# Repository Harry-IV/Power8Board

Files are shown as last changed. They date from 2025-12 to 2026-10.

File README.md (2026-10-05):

# Power8Board V1

48V → 12V Power Distribution & Current-Sensing Board for 8 Thrusters

## Overview

Power8Board is a custom power distribution and sensing PCB intended for robotics applications (e.g. ROVs / AUVs) where 6 DoF control is needed from eight thrusters. 

The board converts 48V DC into 5V and 12V rails, distributes power to eight ESCs, and provides per-thruster current measurement and voltage rail monitoring (3.3, 5, 12, 48) over I²C.

---

## Power Architecture

Two [MPQ860-12V72-L48NBMC](https://www.digikey.com/en/products/detail/murata-power-solutions-inc/MPQ860-12V72-L48NBMC/26005878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) 860W power converters are used to step down 48 to 12V with high efficiency. This 12V power is then routed to eight XT30U-M connectors which ESCs can then connect to for power. These were chosen due to having four power pins, allowing for better heat distribution, and for their active current sharing capabilities. With ~1500W (not 1720 due to drop in max wattage output when current sharing), eight standard T200 thrusters can be driven at full power. This 12V can also be used to power other 12V devices using the [MR30 connector](https://www.tme.com/us/en-us/details/mr30pw-m/dc-power-connectors/amass/) on the board. 

Additionally, a [UWS-5/10-Q48N-C](https://www.digikey.com/en/products/detail/murata-power-solutions-inc/UWS-5-10-Q48N-C/3041704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) 100W power converter is used to step down 48V to 5V. This 5V is outputted through the MR30 and can be used to power a Raspberry Pi for instance.

---

## Current Sensing

Monitor thruster load and detect abnormal conditions (e.g. over-current):

### Current-Sense Amplifiers
  * [INA240A2](https://www.ti.com/product/INA240) (analog)
  * One per ESC channel
  * 50x amplification value (50V/V gain)
* 0.0033 $\Omega$ shunt resistor placed in series with each 12V output
  * Scale factor: 1 / (SHUNT_VALUE * AMP_FACTOR) = 1 / (0.0033 * 50) = 6.061
  * current = 6.061 * (output of INA240)
* Analog output routed to ADC inputs with RC-filter (680 $\Omega$, 2.2 uF)

### Channel Organization

* Left side: 4 thrusters
* Right side: 4 thrusters
* Each side feeds into its own ADC, an [ADS1015](https://www.ti.com/product/ADS1015) (12-bit, I²C interfacing)
* I²C address:
  * Left: 0x48
  * Right: 0x49

---

## Voltage Sensing

Monitor that voltage rails are within normal bounds.

### Power Rails

| Rail  | Purpose |
| ----- | --- |
| 48 V  | Main input power |
| 12 V  | ESC & thruster power |
| 5 V | Miscellaneous |
| 3.3 V | ADCs, current sensors, I²C |

### ADC

* [ADS1015](https://www.ti.com/product/ADS1015) (12-bit, I²C interfacing)
  * Used for measuring the voltages
  * Address: 0x4A

### Voltage Dividers



### Scalar Values
  * 48V: (470+25)/25 = 19.8
  * 12V: (470+110)/110 = 5.273
  * 5V: (470+470)/470 = 2
  * 3.3V: (470+470)/470 = 2

Multiply these values read from the ADC by these scalars respectively to find their true voltages.

---

## LED Indicators

| Rail  | Color |
| ----- | --- |
| 48 V  | Green |
| 12 V  | Yellow |
| 5 V | Red |
| 3.3 V | Amber |

---

## PCB Layout

### 6-layer stackup

| Layer | Type |
| ----- | --- |
| 1 | Signal |
| 2 | Ground |
| 3 | Signal - Power (3.3V) |
| 4 | Power (12V & 48V) |
| 5 | Ground |
| 6 | Signal |



### Design notes

* Nearly all analog traces are routed on layer 3 to reduce effects of digital noise.
* Copper pours help with thermal dissipation.
* Via-in-pad is used to condense routing. It's also a standard option for 6-layer boards when ordering with JLCPCB.
* Ground on layer 2 & 5 provides low-impedance return path and reduce EMI.
* Power converters connect from the backside. 

---

## Ordering

To order, navigate to Power8Board V1/Export. Use Power8Board V1.zip for ordering the PCB and Power8Board V1 Stencil.zip for ordering a stencil (very helpful for soldering). Here are the options I chose when ordering from JLCPCB:



For ordering the components, navigate to Power8Board V1/bom and click on ibom.html. This BOM is interactive, making it great for ordering and knowing where components go while soldering. **Note that this does not include all components for making the board.** This is because pin receptacles are soldered onto the pads for all power converters. Here are the two types of pin receptacles used on the board:

Pin #1: https://www.digikey.com/en/products/detail/mill-max-manufacturing-corp/0372-0-15-15-13-27-10-0/433860

Pin #2: https://www.digikey.com/en/products/detail/mill-max-manufacturing-corp/0312-0-15-15-34-27-10-0/433567

Pin #1 is used on pads 4, 5, 7, and 8 on both 48V-12V converters and on pads 4 and 8 on the 48V-5V converter (10 in total)

Pin #2 is used on pads 1, 2, and 3 on both 48V-12V converters and on pads 1, 2, 3, 5, 6, and 7 on the 48V-5V converter (12 in total)

---

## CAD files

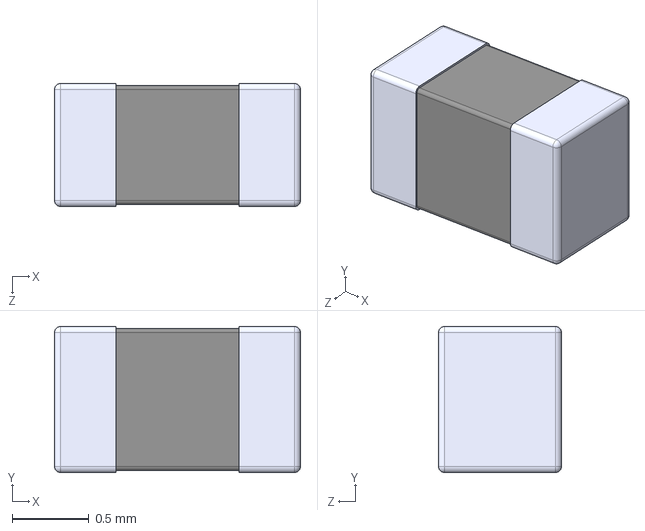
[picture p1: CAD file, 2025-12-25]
Power8Board V1/Components/0603 Ferrite Bead/BLM18KG102SZ1D.step
1.60 x 0.95 x 0.8 mm

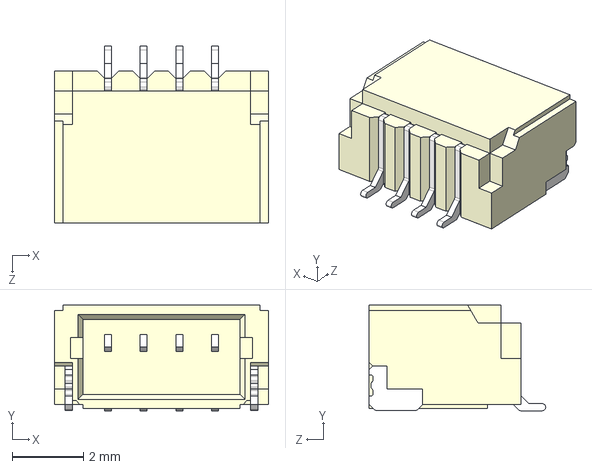
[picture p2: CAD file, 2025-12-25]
Power8Board V1/Components/QWIIC Connector RA/QWIIC Connector RA.step
6.00 x 2.96 x 4.95 mm

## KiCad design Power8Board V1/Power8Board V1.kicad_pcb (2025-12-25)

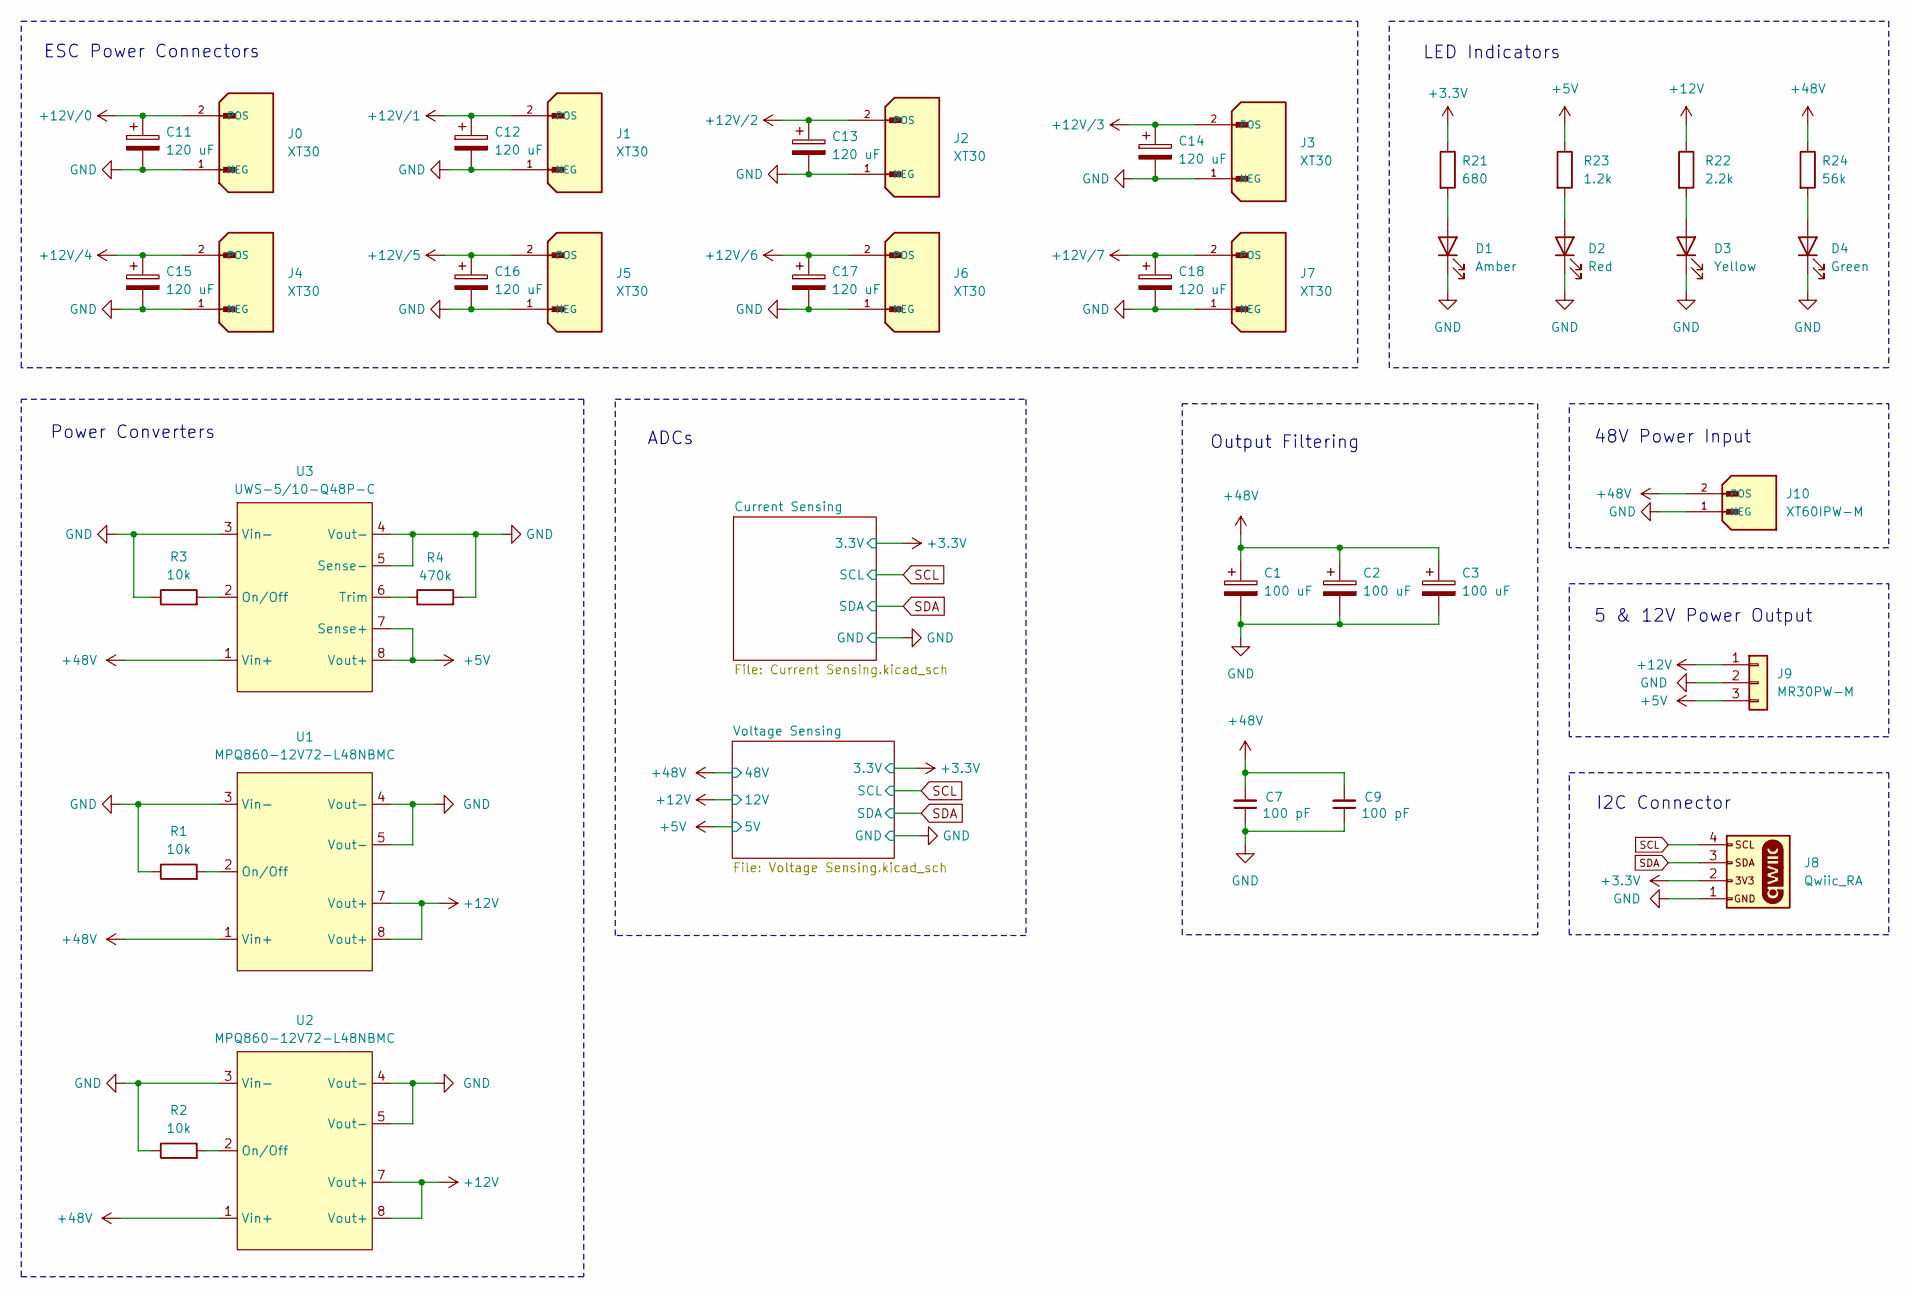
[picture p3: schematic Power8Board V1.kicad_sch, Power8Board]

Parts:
C1, C2, C3: 100 uF; CAP_AVG-8x12_ILC; Part # 107AVG063MFBJ
C7, C9: 100 pF; CAPC2012X140N; Part # KGQ21HCG2A101JT
C11, C12, C13, C14, C15, C16, C17, C18: 120 uF; PCAP_SVP_C6_PAN-M; Part # 20SVPF120M
D1: Amber; WL-SMCW_0805; Part # 150080AS75000
D2: Red; WL-SMCW_0805; Part # 150080RS75000
D3: Yellow; WL-SMCW_0805; Part # 150080YS75000
D4: Green; WL-SMCW_0805; Part # 150080GS75000
J0, J1, J2, J3, J4, J5, J6, J7: XT30; AMASS_XT30U-M_1x02_P5.0mm_Vertical; Part # XT30U-M
J8: Qwiic_RA; QWIIC Connector RA; Part # SM04B-SRSS-TB
J9: MR30PW-M; AMASS_MR30PW-M_1x03_P3.50mm_Horizontal; Part # MR30PW-M
J10: XT60IPW-M; AMASS_XT60IPW-M_1x03_P7.20mm_Horizontal; Part # XT60IPW-M
R1, R2, R3: 10k; R_0805_2012Metric; Part # CRGCQ0805F10K
R4: 470k; R_0805_2012Metric; Part # CRGCQ0805F470K
R21: 680; R_0805_2012Metric; Part # CRGCQ0805F680R
R22: 2.2k; R_0805_2012Metric; Part # CRGCQ0805F2K2
R23: 1.2k; R_0805_2012Metric; Part # CRGCQ0805F1K2
R24: 56k; R_0805_2012Metric; Part # CRGCQ0805F56K
U1, U2: MPQ860-12V72-L48NBMC; Part # MPQ860-12V72-L48NBMC
U3: UWS-5_10-Q48; Part # UWS-5/10-Q48P-C

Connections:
+3.3V: J8.2, R21.1; also elsewhere on the board
+5V: J9.3, R23.1, U3.7 (Sense+), U3.8 (Vout+); also elsewhere on the board
+12V: J9.1, R22.1, U1.7 (Vout+), U1.8 (Vout+), U2.7 (Vout+), U2.8 (Vout+); also elsewhere on the board
+12V/0: C11.1, J0.2 (POS); also elsewhere on the board
+12V/1: C12.1, J1.2 (POS); also elsewhere on the board
+12V/2: C13.1, J2.2 (POS); also elsewhere on the board
+12V/3: C14.1, J3.2 (POS); also elsewhere on the board
+12V/4: C15.1, J4.2 (POS); also elsewhere on the board
+12V/5: C16.1, J5.2 (POS); also elsewhere on the board
+12V/6: C17.1, J6.2 (POS); also elsewhere on the board
+12V/7: C18.1, J7.2 (POS); also elsewhere on the board
+48V: C1.1, C2.1, C3.1, C7.2, C9.2, J10.2 (POS), R24.1, U1.1 (Vin+), U2.1 (Vin+), U3.1 (Vin+); also elsewhere on the board
GND: C1.2, C2.2, C3.2, C7.1, C9.1, C11.2, C12.2, C13.2, C14.2, C15.2, C16.2, C17.2, C18.2, D1.1 (K), D2.1 (K), D3.1 (K), D4.1 (K), J0.1 (NEG), J1.1 (NEG), J2.1 (NEG), J3.1 (NEG), J4.1 (NEG), J5.1 (NEG), J6.1 (NEG), J7.1 (NEG), J8.1, J9.2, J10.1 (NEG), R1.1, R2.1, R3.1, R4.2, U1.3 (Vin-), U1.4 (Vout-), U1.5 (Vout-), U2.3 (Vin-), U2.4 (Vout-), U2.5 (Vout-), U3.3 (Vin-), U3.4 (Vout-), U3.5 (Sense-); also elsewhere on the board
unnamed: D1.2 (A), R21.2
unnamed: D2.2 (A), R23.2
unnamed: D3.2 (A), R22.2
unnamed: D4.2 (A), R24.2
unnamed: R1.2, U1.2 (On/Off)
unnamed: R2.2, U2.2 (On/Off)
unnamed: R3.2, U3.2 (On/Off)
unnamed: R4.1, U3.6 (Trim)
SCL: J8.4; also elsewhere on the board
SDA: J8.3; also elsewhere on the board

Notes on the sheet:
I2C Connector
LED Indicators
48V Power Input
ADCs
Power Converters
Output Filtering
5 & 12V Power Output
ESC Power Connectors

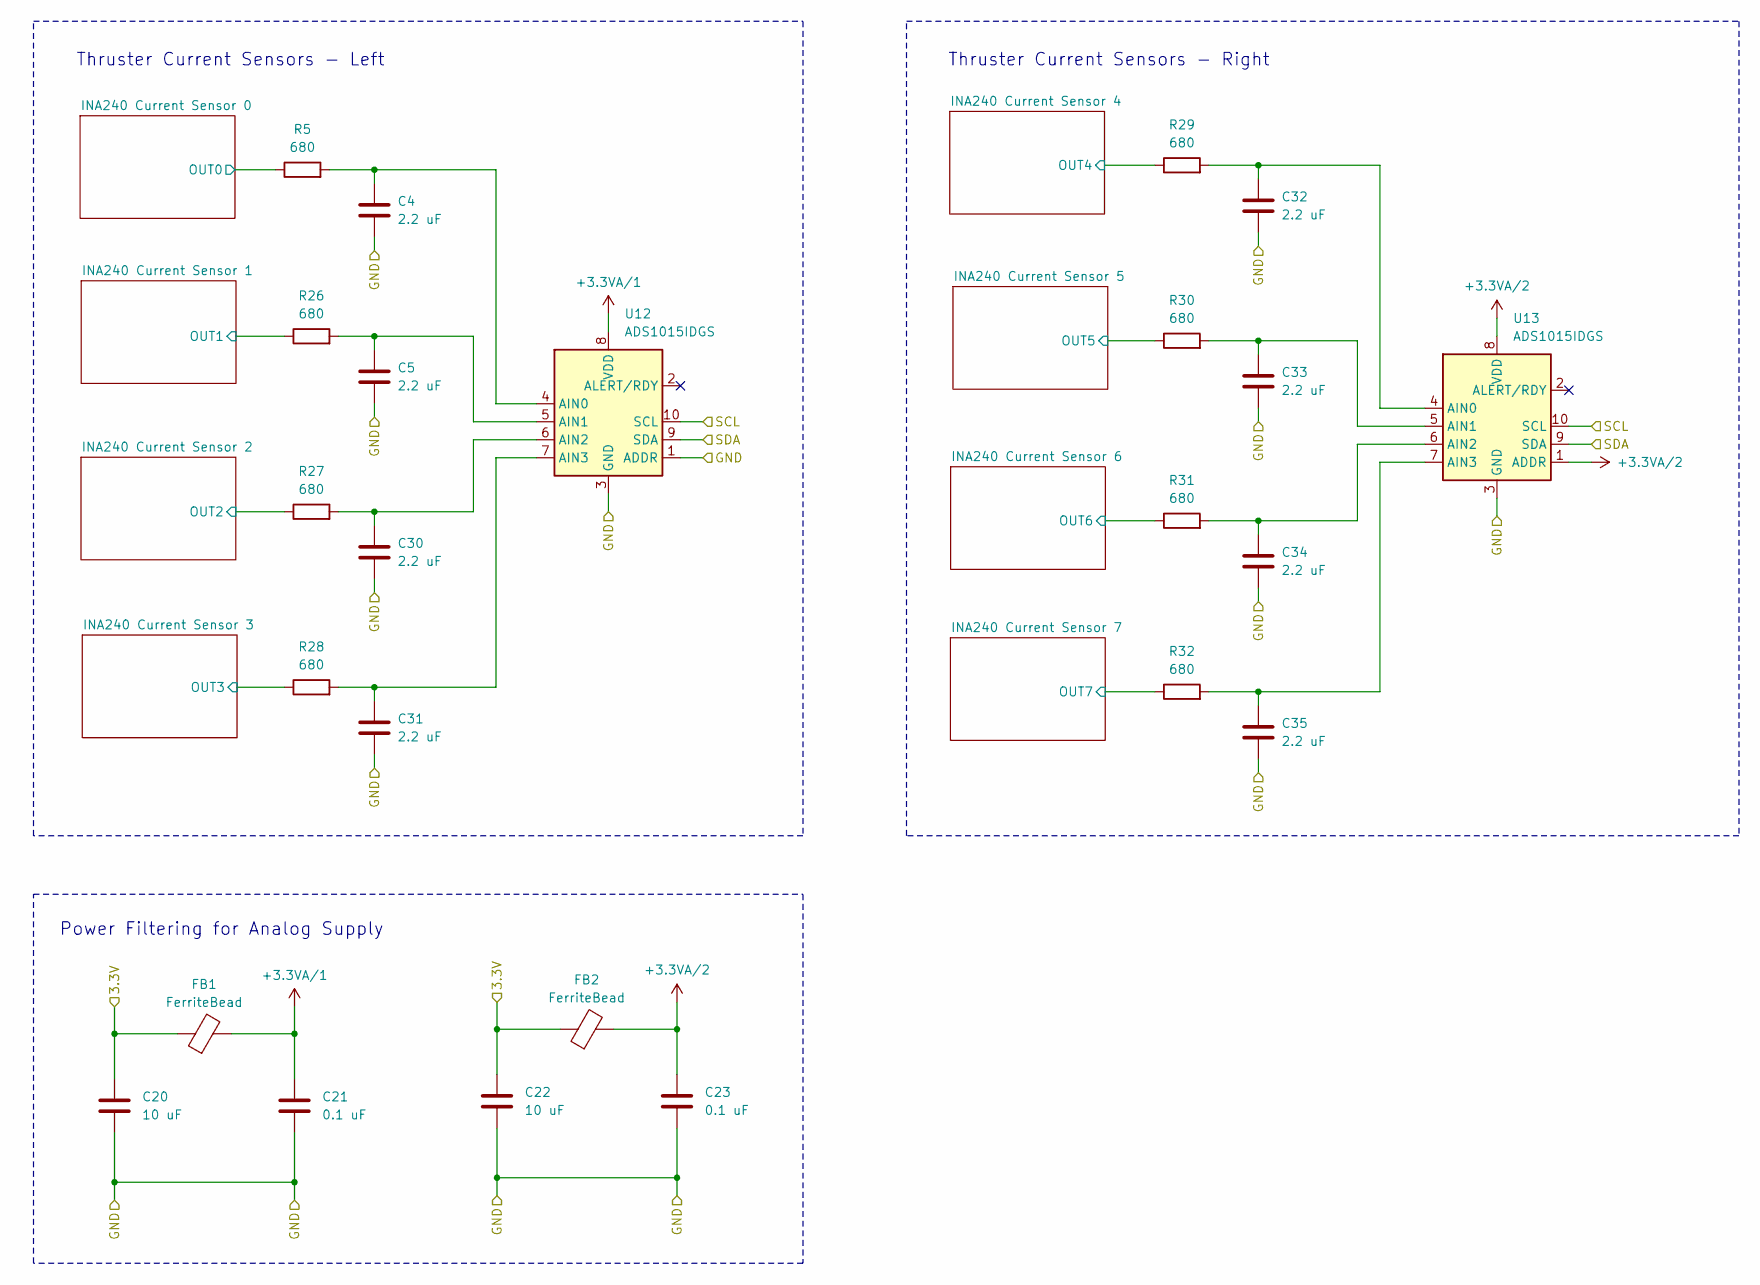
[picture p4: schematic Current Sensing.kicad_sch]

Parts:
C4, C5, C30, C31, C32, C33, C34, C35: 2.2 uF; C_0603_1608Metric; Part # GRM188Z71E225KE43D
C20, C22: 10 uF; C_0603_1608Metric; Part # GRM188R61E106KA73D
C21, C23: 0.1 uF; C_0603_1608Metric; Part # C0603C104K5RACTU
FB1, FB2: FerriteBead; 0603 Ferrite Bead; Part # BLM18KG102SZ1D
R5, R26, R27, R28, R29, R30, R31, R32: 680; R_0603_1608Metric; Part # CRGCQ0603F680R
U12, U13: ADS1015IDGS; TSSOP-10_3x3mm_P0.5mm; Part # ADS1015IDGSR

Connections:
+3.3V: C20.1, C22.1, FB1.1, FB2.1; also elsewhere on the board
+3.3VA/1: C21.1, FB1.2, U12.8 (VDD)
+3.3VA/2: C23.1, FB2.2, U13.1 (ADDR), U13.8 (VDD)
/Current Sensing/INA240 Current Sensor 0/OUT0: R5.1; also elsewhere on the board
/Current Sensing/INA240 Current Sensor 1/OUT1: R26.1; also elsewhere on the board
/Current Sensing/INA240 Current Sensor 2/OUT2: R27.1; also elsewhere on the board
/Current Sensing/INA240 Current Sensor 3/OUT3: R28.1; also elsewhere on the board
/Current Sensing/INA240 Current Sensor 4/OUT4: R29.1; also elsewhere on the board
/Current Sensing/INA240 Current Sensor 5/OUT5: R30.1; also elsewhere on the board
/Current Sensing/INA240 Current Sensor 6/OUT6: R31.1; also elsewhere on the board
/Current Sensing/INA240 Current Sensor 7/OUT7: R32.1; also elsewhere on the board
GND: C4.2, C5.2, C20.2, C21.2, C22.2, C23.2, C30.2, C31.2, C32.2, C33.2, C34.2, C35.2, U12.1 (ADDR), U12.3 (GND), U13.3 (GND); also elsewhere on the board
unnamed: C4.1, R5.2, U12.4 (AIN0)
unnamed: C5.1, R26.2, U12.5 (AIN1)
unnamed: C30.1, R27.2, U12.6 (AIN2)
unnamed: C31.1, R28.2, U12.7 (AIN3)
unnamed: C32.1, R29.2, U13.4 (AIN0)
unnamed: C33.1, R30.2, U13.5 (AIN1)
unnamed: C34.1, R31.2, U13.6 (AIN2)
unnamed: C35.1, R32.2, U13.7 (AIN3)
SCL: U12.10 (SCL), U13.10 (SCL); also elsewhere on the board
SDA: U12.9 (SDA), U13.9 (SDA); also elsewhere on the board

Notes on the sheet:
Thruster Current Sensors - Right
Power Filtering for Analog Supply
Thruster Current Sensors - Left

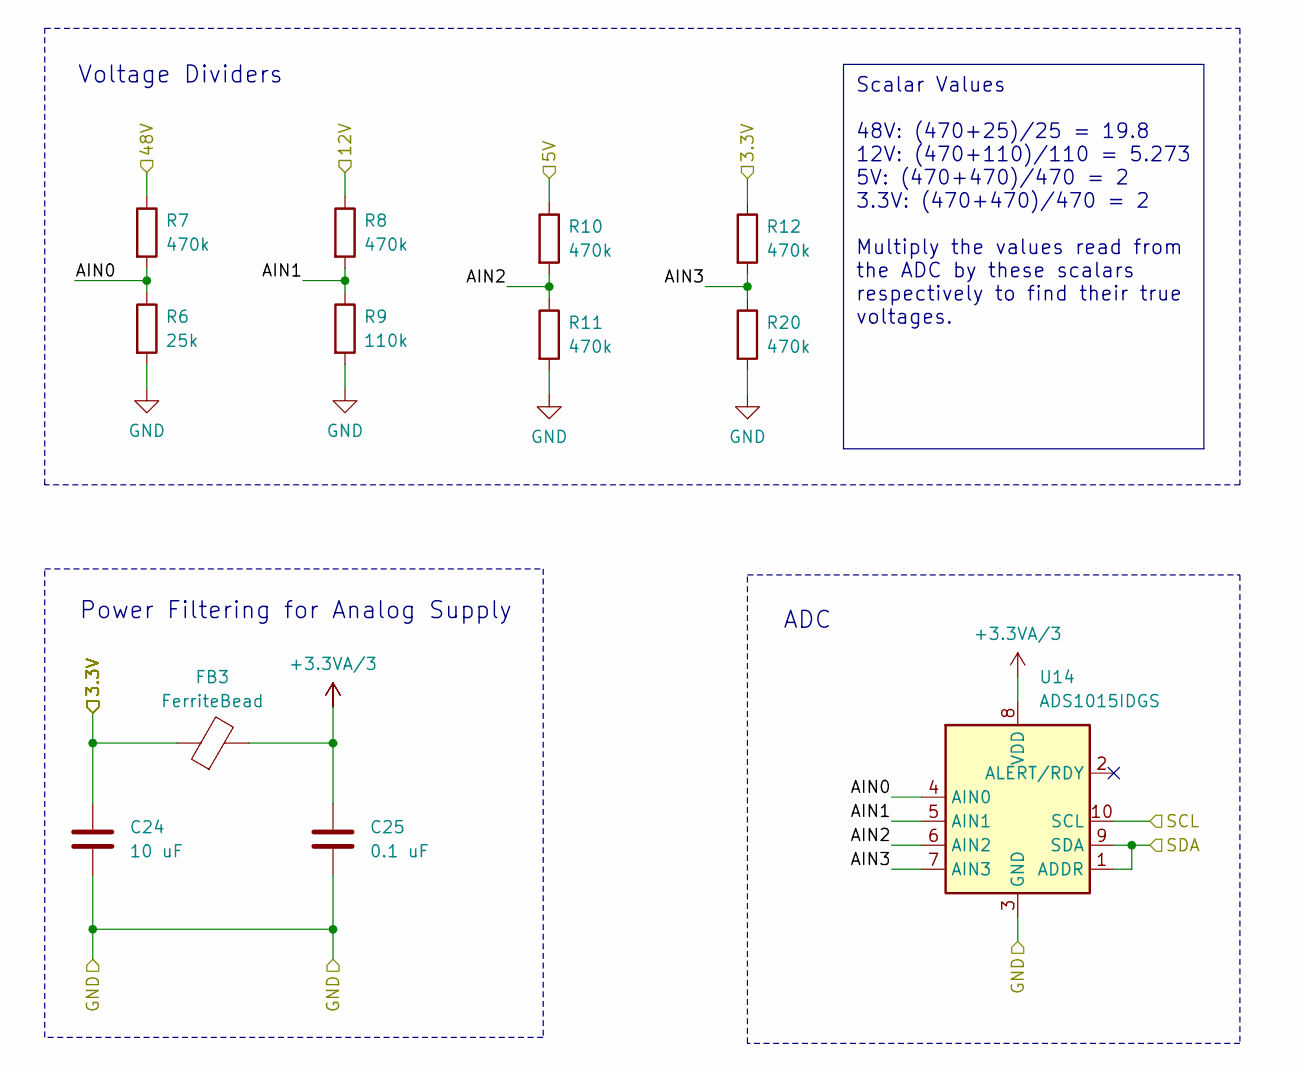
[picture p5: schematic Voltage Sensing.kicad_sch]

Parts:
C24: 10 uF; C_0805_2012Metric; Part # GRT21BC71E106KE13L
C25: 0.1 uF; C_0805_2012Metric; Part # C0805C104J5RACAUTO
FB3: FerriteBead; BEADC2012X105N; Part # MPZ2012S102ATD25
R6: 25k; R_0805_2012Metric; Part # CPF-A-0805B25KE
R7, R8, R10, R11, R12, R20: 470k; RES_TNPW0805_VIS; Part # TNPW0805470KBEEA
R9: 110k; R_0805_2012Metric; Part # RQ73C2A110KBTDF
U14: ADS1015IDGS; TSSOP-10_3x3mm_P0.5mm; Part # ADS1015IDGSR

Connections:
+3.3V: C24.1, FB3.1, R12.1; also elsewhere on the board
+3.3VA/3: C25.1, FB3.2, U14.8 (VDD)
+5V: R10.1; also elsewhere on the board
+12V: R8.1; also elsewhere on the board
+48V: R7.1; also elsewhere on the board
/Voltage Sensing/AIN0: R6.1, R7.2, U14.4 (AIN0)
/Voltage Sensing/AIN1: R8.2, R9.1, U14.5 (AIN1)
/Voltage Sensing/AIN2: R10.2, R11.1, U14.6 (AIN2)
/Voltage Sensing/AIN3: R12.2, R20.1, U14.7 (AIN3)
GND: C24.2, C25.2, R6.2, R9.2, R11.2, R20.2, U14.3 (GND); also elsewhere on the board
SCL: U14.10 (SCL); also elsewhere on the board
SDA: U14.1 (ADDR), U14.9 (SDA); also elsewhere on the board

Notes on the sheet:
Scalar Values 48V: (470+25)/25 = 19.8 12V: (470+110)/110 = 5.273 5V: (470+470)/470 = 2 3.3V: (470+470)/470 = 2 Multiply the values read from the ADC by these scalars respectively to find their true voltages.
ADC
Power Filtering for Analog Supply
Voltage Dividers

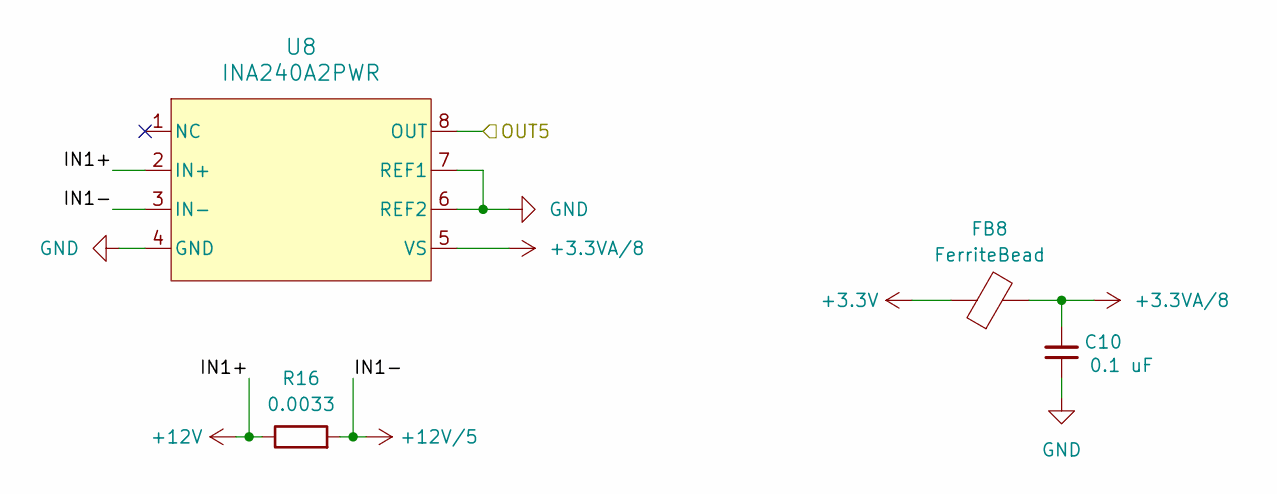
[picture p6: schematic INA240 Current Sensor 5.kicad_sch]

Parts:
C10: 0.1 uF; CAPC2012X140N; Part # C0805C104J5RACAUTO
FB8: FerriteBead; BEADC2012X105N; Part # MPZ2012S102ATD25
R16: 0.0033; RES_VISHAY_WSLP2512_A_VIS; Part # WSLP25123L300DEA
U8: INA240A2PWR; PW0008A_M; Part # INA240A2PWR

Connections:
+3.3V: FB8.1; also elsewhere on the board
+3.3VA/8: C10.2, FB8.2, U8.5 (VS)
+12V: R16.1, U8.2 (IN+); also elsewhere on the board
+12V/5: R16.2, U8.3 (IN-); also elsewhere on the board
/Current Sensing/INA240 Current Sensor 5/OUT5: U8.8 (OUT); also elsewhere on the board
GND: C10.1, U8.4 (GND), U8.6 (REF2), U8.7 (REF1); also elsewhere on the board

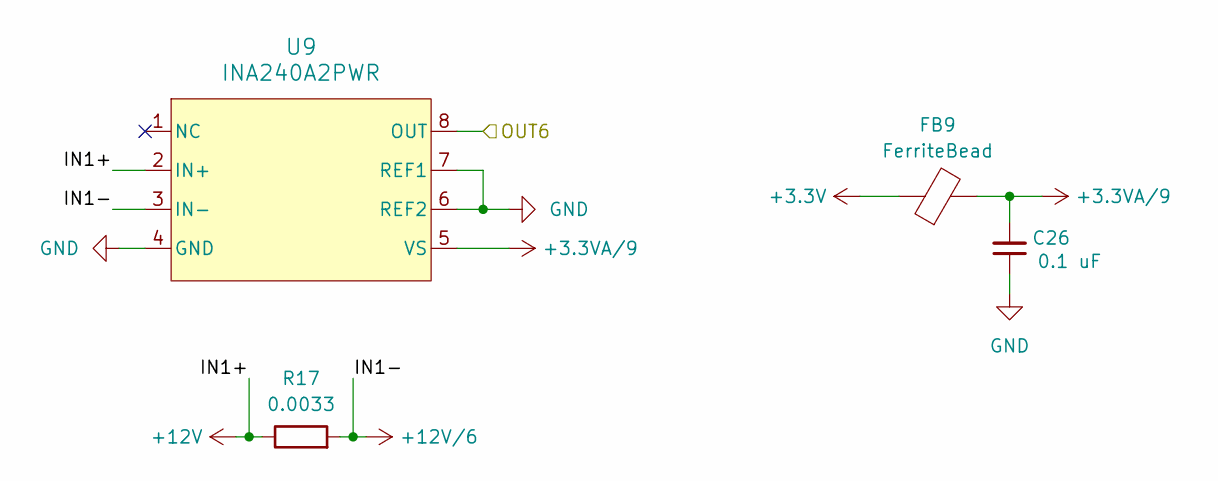
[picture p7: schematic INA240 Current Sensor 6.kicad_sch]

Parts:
C26: 0.1 uF; CAPC2012X140N; Part # C0805C104J5RACAUTO
FB9: FerriteBead; BEADC2012X105N; Part # MPZ2012S102ATD25
R17: 0.0033; RES_VISHAY_WSLP2512_A_VIS; Part # WSLP25123L300DEA
U9: INA240A2PWR; PW0008A_M; Part # INA240A2PWR

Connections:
+3.3V: FB9.1; also elsewhere on the board
+3.3VA/9: C26.2, FB9.2, U9.5 (VS)
+12V: R17.1, U9.2 (IN+); also elsewhere on the board
+12V/6: R17.2, U9.3 (IN-); also elsewhere on the board
/Current Sensing/INA240 Current Sensor 6/OUT6: U9.8 (OUT); also elsewhere on the board
GND: C26.1, U9.4 (GND), U9.6 (REF2), U9.7 (REF1); also elsewhere on the board

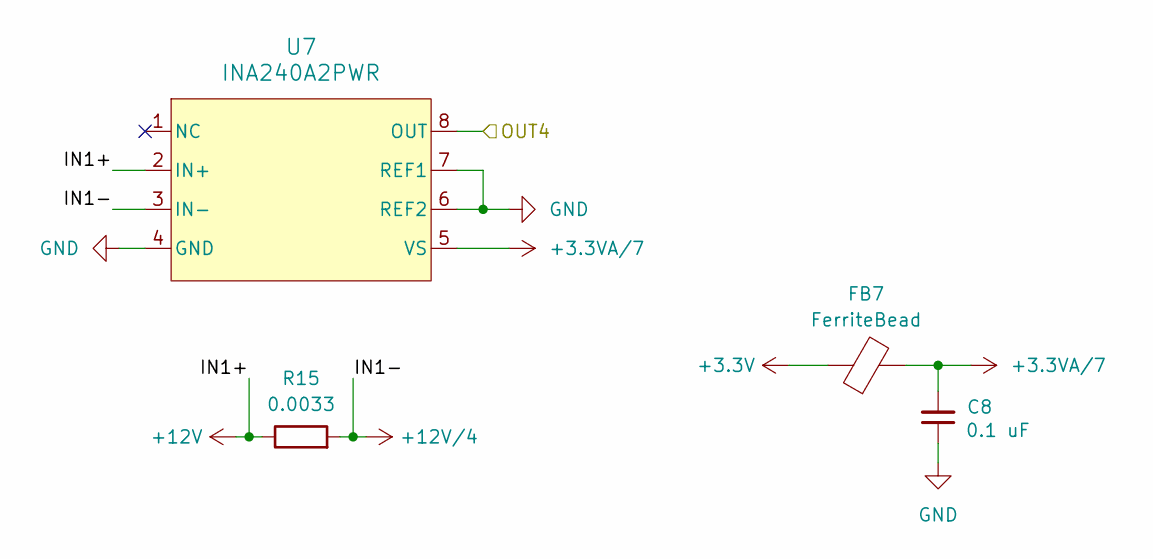
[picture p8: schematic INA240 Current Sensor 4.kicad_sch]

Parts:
C8: 0.1 uF; CAPC2012X140N; Part # C0805C104J5RACAUTO
FB7: FerriteBead; BEADC2012X105N; Part # MPZ2012S102ATD25
R15: 0.0033; RES_VISHAY_WSLP2512_A_VIS; Part # WSLP25123L300DEA
U7: INA240A2PWR; PW0008A_M; Part # INA240A2PWR

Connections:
+3.3V: FB7.1; also elsewhere on the board
+3.3VA/7: C8.2, FB7.2, U7.5 (VS)
+12V: R15.1, U7.2 (IN+); also elsewhere on the board
+12V/4: R15.2, U7.3 (IN-); also elsewhere on the board
/Current Sensing/INA240 Current Sensor 4/OUT4: U7.8 (OUT); also elsewhere on the board
GND: C8.1, U7.4 (GND), U7.6 (REF2), U7.7 (REF1); also elsewhere on the board

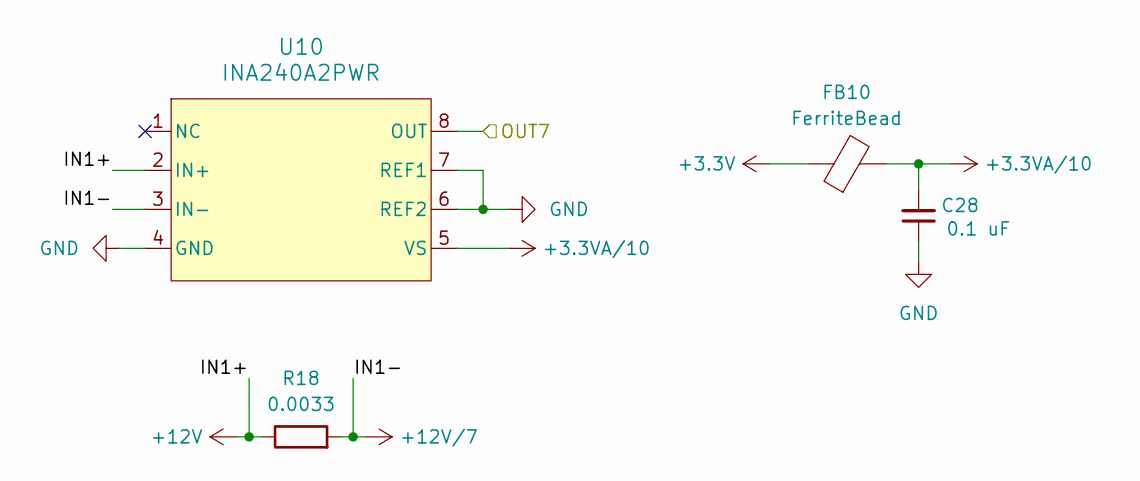
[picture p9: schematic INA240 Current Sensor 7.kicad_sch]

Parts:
C28: 0.1 uF; CAPC2012X140N; Part # C0805C104J5RACAUTO
FB10: FerriteBead; BEADC2012X105N; Part # MPZ2012S102ATD25
R18: 0.0033; RES_VISHAY_WSLP2512_A_VIS; Part # WSLP25123L300DEA
U10: INA240A2PWR; PW0008A_M; Part # INA240A2PWR

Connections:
+3.3V: FB10.1; also elsewhere on the board
+3.3VA/10: C28.2, FB10.2, U10.5 (VS)
+12V: R18.1, U10.2 (IN+); also elsewhere on the board
+12V/7: R18.2, U10.3 (IN-); also elsewhere on the board
/Current Sensing/INA240 Current Sensor 7/OUT7: U10.8 (OUT); also elsewhere on the board
GND: C28.1, U10.4 (GND), U10.6 (REF2), U10.7 (REF1); also elsewhere on the board

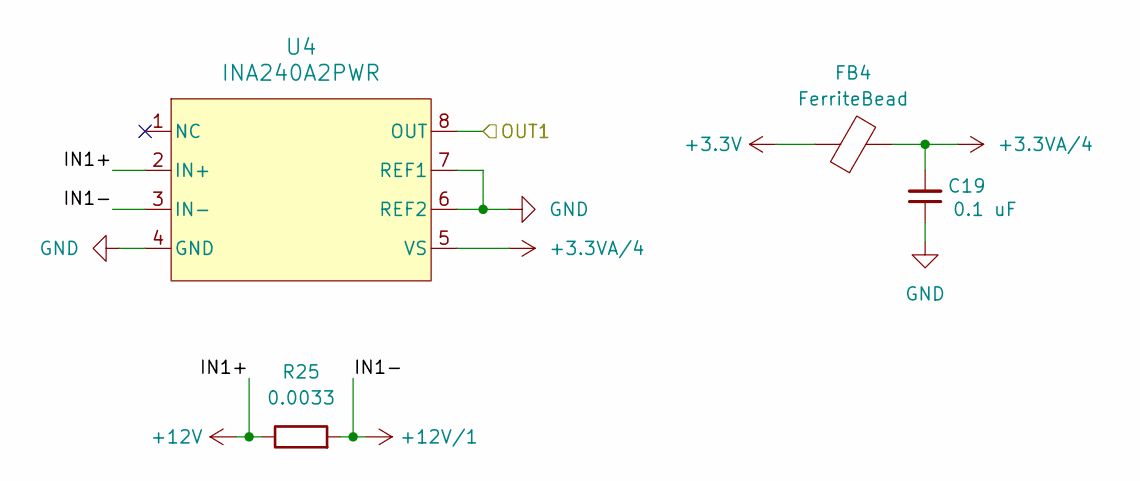
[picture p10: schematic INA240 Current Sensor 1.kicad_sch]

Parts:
C19: 0.1 uF; CAPC2012X140N; Part # C0805C104J5RACAUTO
FB4: FerriteBead; BEADC2012X105N; Part # MPZ2012S102ATD25
R25: 0.0033; RES_VISHAY_WSLP2512_A_VIS; Part # WSLP25123L300DEA
U4: INA240A2PWR; PW0008A_M; Part # INA240A2PWR

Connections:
+3.3V: FB4.1; also elsewhere on the board
+3.3VA/4: C19.2, FB4.2, U4.5 (VS)
+12V: R25.1, U4.2 (IN+); also elsewhere on the board
+12V/1: R25.2, U4.3 (IN-); also elsewhere on the board
/Current Sensing/INA240 Current Sensor 1/OUT1: U4.8 (OUT); also elsewhere on the board
GND: C19.1, U4.4 (GND), U4.6 (REF2), U4.7 (REF1); also elsewhere on the board

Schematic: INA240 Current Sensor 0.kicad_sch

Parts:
C29: 0.1 uF; CAPC2012X140N; Part # C0805C104J5RACAUTO
FB11: FerriteBead; BEADC2012X105N; Part # MPZ2012S102ATD25
R19: 0.0033; RES_VISHAY_WSLP2512_A_VIS; Part # WSLP25123L300DEA
U11: INA240A2PWR; PW0008A_M; Part # INA240A2PWR

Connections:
+3.3V: FB11.1; also elsewhere on the board
+3.3VA/11: C29.2, FB11.2, U11.5 (VS)
+12V: R19.1, U11.2 (IN+); also elsewhere on the board
+12V/0: R19.2, U11.3 (IN-); also elsewhere on the board
/Current Sensing/INA240 Current Sensor 0/OUT0: U11.8 (OUT); also elsewhere on the board
GND: C29.1, U11.4 (GND), U11.6 (REF2), U11.7 (REF1); also elsewhere on the board

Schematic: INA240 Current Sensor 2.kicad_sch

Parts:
C27: 0.1 uF; CAPC2012X140N; Part # C0805C104J5RACAUTO
FB5: FerriteBead; BEADC2012X105N; Part # MPZ2012S102ATD25
R13: 0.0033; RES_VISHAY_WSLP2512_A_VIS; Part # WSLP25123L300DEA
U5: INA240A2PWR; PW0008A_M; Part # INA240A2PWR

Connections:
+3.3V: FB5.1; also elsewhere on the board
+3.3VA/5: C27.2, FB5.2, U5.5 (VS)
+12V: R13.1, U5.2 (IN+); also elsewhere on the board
+12V/2: R13.2, U5.3 (IN-); also elsewhere on the board
/Current Sensing/INA240 Current Sensor 2/OUT2: U5.8 (OUT); also elsewhere on the board
GND: C27.1, U5.4 (GND), U5.6 (REF2), U5.7 (REF1); also elsewhere on the board

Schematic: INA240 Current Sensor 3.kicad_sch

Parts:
C6: 0.1 uF; CAPC2012X140N; Part # C0805C104J5RACAUTO
FB6: FerriteBead; BEADC2012X105N; Part # MPZ2012S102ATD25
R14: 0.0033; RES_VISHAY_WSLP2512_A_VIS; Part # WSLP25123L300DEA
U6: INA240A2PWR; PW0008A_M; Part # INA240A2PWR

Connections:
+3.3V: FB6.1; also elsewhere on the board
+3.3VA/6: C6.2, FB6.2, U6.5 (VS)
+12V: R14.1, U6.2 (IN+); also elsewhere on the board
+12V/3: R14.2, U6.3 (IN-); also elsewhere on the board
/Current Sensing/INA240 Current Sensor 3/OUT3: U6.8 (OUT); also elsewhere on the board
GND: C6.1, U6.4 (GND), U6.6 (REF2), U6.7 (REF1); also elsewhere on the board

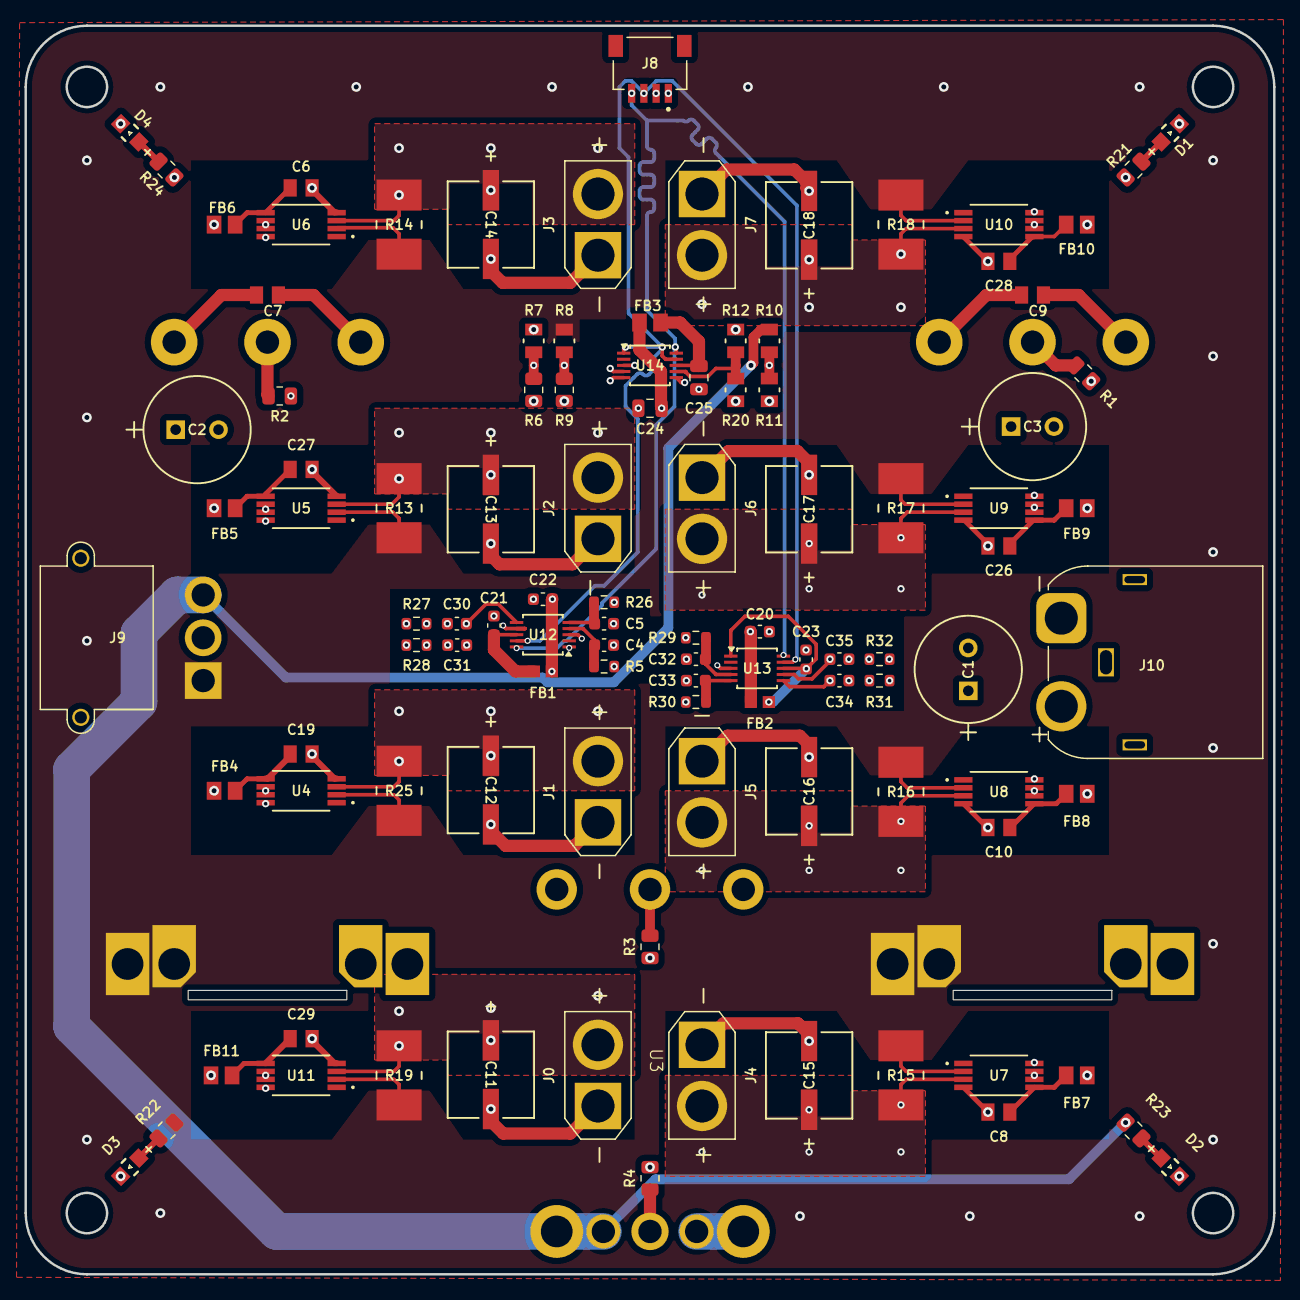
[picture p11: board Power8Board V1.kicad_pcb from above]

Board: 6 copper layers, 102.0 x 102.0 mm, 107 parts (0 on the bottom side), 54 nets.

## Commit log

2025-08-12 Progress up to 8/11/2025.
    [Power8Board V1.kicad_pcb, Power8Board V1.kicad_sch]
2025-08-26 Added voltage and current sensing.
    [ADC Current Sensors.kicad_sch, ADS1015 ADC.kicad_sch, Current Sensing.kicad_sch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]
2025-08-28 Added power indicator LEDs.
    [Power8Board V1.kicad_sch, Voltage Sensing.kicad_sch]
2025-08-29 Design before laying out.
    [INA240 Current Sensor 2.kicad_sch, Power8Board V1.kicad_sch]
2025-08-30 Beginning to layout.
    [Current Sensing.kicad_sch, Power8Board V1.kicad_pcb, Power8Board V1.kicad_sch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]
2025-09-01 There is a general layout.
    [Power8Board V1.kicad_pcb, Power8Board V1.kicad_sch]
2025-09-04 Laid out components
    [Current Sensing.kicad_sch, INA240 Current Sensor 0.kicad_sch, INA240 Current Sensor 1.kicad_sch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]
2025-09-05 Laying out 9/5.
    [Power8Board V1.kicad_pcb]
2025-09-06 About half a side is done.
    [Power8Board V1.kicad_pcb]
2025-09-08 Switched out input capacitors.
    [Power8Board V1.kicad_pcb, Power8Board V1.kicad_sch]
2025-09-20 Added 0603 components and RC filters.
    [Current Sensing.kicad_sch, Power8Board V1.kicad_pcb]
2025-09-23 9/22 Progress
    [Current Sensing.kicad_sch, Power8Board V1.kicad_pcb]
2025-09-23 9/23 Progress
    [Power8Board V1.kicad_pcb]
2025-09-24 DRC sorted out.
    [Current Sensing.kicad_sch, INA240 Current Sensor 1.kicad_sch, Power8Board V1.kicad_pcb]
2025-09-25 PCB before BOM creation.
    [Power8Board V1.kicad_pcb]
2025-09-26 Ordered PCB.
    [Power8Board V1-B_Cu.gbl, Power8Board V1-B_Mask.gbs, Power8Board V1-B_Paste.gbp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]
2025-09-29 Includes most recent BOM.
    [Power8Board V1.kicad_pcb, Voltage Sensing.kicad_sch]
2025-12-25 Added boxes in schematic for organization.
    [Current Sensing.kicad_sch, Power8Board V1.kicad_pcb, Power8Board V1.kicad_sch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]
2025-12-25 Moved current sensor schematics to Current Sensor folder.
    [Current Sensing.kicad_sch, INA240 Current Sensor 0.kicad_sch, INA240 Current Sensor 1.kicad_sch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]
2025-12-25 Added non KiCad standard components in Components folder.
    [BLM18KG102SZ1D.step, Current Sensing.kicad_sch, INA240 Current Sensor 7.kicad_sch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]
2025-12-25 Removed KiCad generated files and backups from tracking.
2025-12-26 Added README
    Added detailed documentation for the Power8Board V1, including power architecture, current sensing, voltage sensing, LED indicators, PCB layout, and ordering instructions.
